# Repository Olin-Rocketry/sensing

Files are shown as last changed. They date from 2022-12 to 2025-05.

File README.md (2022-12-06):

# Sensing

Repository for all Olin Rocketry hardware and firmware.

The purpose of the avionics system is to determine when to deploy the drogue and main chutes, and to send the signal to do so to the recovery system. The flight computer contains several sensors to help detect apogee, and a microcontroller to read and process the data and send the signal.

The avionics system consists of

- a commercial-off-the-shelf (COTS) flight computer;
- a student-designed flight computer, which includes sensors, microcontroller, GPS, and radio; and
- a student-designed battery management system (BMS).

The COTS computer is a **\_** model. It has its own batteries, sensors, and radio and can trigger the recovery system independently. It is intended as a backup and is required by IREC competition rules (partly so they have a reliable altitude measurement for the competition). The BMS is described on the Power Management subteam page. It can suppy a steady 3.3V current up to about 1000 mA to the student-designed flight computer board.

**The flight computer consists of a Teensy 3.6 microcontroller and various sensors.**

- The [Teensy 3.6](https://www.pjrc.com/teensy/card9a_rev1.pdf) is computationally powerful enough for complex data processing, has many interrupt pins, and many pins in general for connecting multiple sensors. It also has a built-in SD card reader. The decision to use it was made before the Fall 2020 semester; other options were considered and may be viable for future iterations. The main drawback of the Teensy 3.6 is its cost, at around $30. This makes having multiple prototypes very expensive, especially if we want to distribute copies to team members living in separate places.
- We considered 3 different inertial measurement units (IMUs, or accelerometers):
  - [ADXL345](https://www.analog.com/media/en/technical-documentation/data-sheets/ADXL345.pdf) is a very common 3-axis accelerometer. It is widely available and was already in stock from JLC, the company manufacturing our board. This means our boards will have the ADXL345 already populated when it is shipped to us, a bonus.
  - [BMI088](https://download.mikroe.com/documents/datasheets/BMI088_Datasheet.pdf) is a 6-axis accelerometer and gyroscope (axes 4-6 are angular acceleration).
  - [BNO055](https://cdn-shop.adafruit.com/datasheets/BST_BNO055_DS000_12.pdf) is a 9-axis accelerometer, relative, and absolute gyroscope (axes 7-9 are absolute orientation).

We designed our Rev1 PCB to hold all three IMUs, so that we could test all of them at once. However, as of ordering time in January, the BMI088 and BNO055 were out of stock at Digikey and Mouser, so these were never tested.

- [MPL3115A2](https://www.nxp.com/docs/en/data-sheet/MPL3115A2.pdf) is a barometer calibrated to provide altimetry. It is the most important sensor, as it allows us to determine our absolute altitude. Our simplest apogee detection is triggered by a certain number of consecutive decreasing altitude measurements.
- Header pins for the [Adafruit Ultimate GPS Breakout (Version 3)](https://www.adafruit.com/product/746?__hstc), a $40 complete GPS module.
- Header pins for the [RFM9X LoRa Packet Radio Breakout](https://learn.adafruit.com/adafruit-rfm69hcw-and-rfm96-rfm95-rfm98-lora-packet-padio-breakouts/arduino-wiring), the currenty preferred radio (see Communications subteam page).

**Rev 1 Testing Update: Spring 2021**

The sensors on Rev1 (the ADXL345 accelerometer and the MPL3115A2 barometer) work, and the data can be read over I2C. The current data format is a csv file with time since launch, x, y, and z acceleration, pressure, altitude, and temperature. The readings from the accelerometer have very little noise when at rest (the only test performed so far - others to follow soon). The barometer has some issues. First of all, it has an offset of about 1.7 atmospheres. When those 1.7 atm are subtracted out, however, it provides high precision and sensitivity. The altitude readings are off by the same offset, as I believe they are calculated from the barometer reading anyway. The temperature has some 20 degrees F offset and significant drift of 2-5 degrees F over a few minutes. More testing to follow.

I looked at the specs and realized that the ADXL345 and MPL3115A2 together consume less than 3 mA of current at their max. Since the Teensy can output 250 mA through those pins, I don’t see why to use an external power source; we can just use the 3.3V pins on the Teensy.
The tests I have done have been using the 3.3V pin as a power source.

**Tests performed 3/26/2021:**

**Power supply test:** Get an external power supply and give 3.3V to the power inputs. Test the test points and the Teensy’s Vin pin. Test data logging onto SD card. Test sensors connected only to external power supply vs. connected to Teensy 3.3V pin vs. connected to both.

**Results:**
The transistor part of the Rev1 power management circuit did not work. For some reason, there was always only ~0.6V on both the gate and drain pins, and so 0.6V on the rest of the PCB. I tried several pin configurations and nothing helped. It worked fine when I bypassed the transistor and powered 3.3V to both the Teensy and the PCB.
The Teensy could not write to the SD card when the PCB and Teensy were powered independently; it only works when the rest of the PCB is powered through the Teensy’s dedicated 3.3V pin. Therefore, I recommend just using the Teensy’s 3.3V pin to power the sensors.

In this case, I suggest the voltage supplied by the BMS should be 3.6V instead of 3.3V, so that the linear voltage regulator on the Teensy can effectively supply the 3.3V to the sensors. Voltage regulators necessariy have a small voltage drop across them, although I came across a [source](https://forum.pjrc.com/threads/55789-Power-Teensy-3-6-with-lipo-battery?p=203568&viewfull=1#post203568) that says the Teensy will bypass its voltage regulator if the voltage is too low, so there is not necessarily an issue.

**MPL3115A2 Accuracy Test:** Take the Rev1 board up and down the stairs of the MAC building 2 times and measure altitude difference.

**Results:**
The readings are inaccurate, yet very precise. The pressure has reads on the order of 200 kPa, which is double what is expected (1 atmosphere is about 100 kPa), and the temperature reads 90 degrees F in a 70 degree room. Yet after the offset is subtracted, the sensor tracks changes in height of less than 20 feet (the distance between floors in the MAC, and the highest resolution analyzed) quite well. The graph below shows the corrected elevation and temperature over the course of my trip up and down the stairs of the MAC, then outside onto the great lawn and up to the 4th floor of West Hall. There is some drift over time as it sat on my desk after “landing,” on the order of 20 feet over 20 minutes. This is worrying, but it will likely not be a problem during a launch lasting a few minutes.

rev1 full schematic

**Developing the Rev 2 board**

With the ADXL345 and MPL3115A2 sensors confirmed to work, the main objective of the Rev 2 board is to make it fit into the avionics bay. The final board is 80mm tall by 72mm wide and has a mounting hole in each corner. The power supply transistor circuit has been replaced with a power multiplexer, a zener diode was added for overvoltage protection, and the power from the BMS goes directly into the Vin pin on the Teensy; the sensors and other circuitry are powered by the Teensy's 3.3V pin as discussed above. Additionally, 5 debugging LEDs, one power LED, and a [buzzer](https://www.digikey.com/en/products/detail/mallory-sonalert-products-inc/PT-1340P-P10-PQ/4996070) have also been added and are controlled by spare digital pins on the Teensy. A 10uF capacitor was added between the power and ground pins of the radio upon testing by the Communications team.

The board has been ordered from JLC and will arrive within a couple days.

## Guide to creating PCBs

**The process for creating the flight computer PCB has multiple stages:**
  1. Components are selected, including the microcontroller and sensors.
  2. Schematics are created for each sensor individually. This mainly involves copying the circuit diagram from the datasheets for each sensor. Every sensor needs at least two capacitors for its power source, and some require external pull-up resistors, for example. The BNO055 is connected to an external crystal oscillator. It’s also a good idea to add test points (basically large, labelled vias) for debugging purposes. We tried to add a test point to every trace on the schematic that would not be directly connected to the microcontroller (because we can access those traces directly through the microcontroller’s pins). 
  3. For the Rev1 board, footprints for the BNO055 and MPL3115A2 were created by copying the dimensions given by the datasheets. The other footprints were downloaded from snapeda.com. In reality, the only reason to create them manually is to get practice with KiCAD, which is why it was done this way for two of the sensors; in future, snapeda.com likely has all the footprints we will need, without the possibility of human error.*
  4. At this stage, layouts are also created for the supporting circuitry surrounding each sensor individually. These layouts will be manually recreated later, but it is easier to go through a few iterations to find the optimal footprint placements now, before all the layouts are combined on one board.
  5. Now, all of the individual schematics are moved into one place. This can be done in the KiCAD schematic editor (eeschema) by clicking File -> Append Schematic Sheet Content -> then navigate to the schematic to import and click Use Relative Path.
  6. Now all the schematics can be hooked up together; in this case it means connecting each sensor’s communication pins to the Teensy and power and ground to the power supply. A small circuit for regulating the power supply from the BMS, as well as header pins for the BMS and GPS and radio breakout boards are also added to this schematic.
  7. Review the schematics with the flight computer sub-team. Hopefully we have been checking in all along, but now is the last chance to make changes before a lot of work goes into the layout. After this, even small changes to the schematic can be very hard to implement in the layout without starting over.
  8. The layout of all the components for the final PCB is created. You cannot copy and paste the layouts created earlier for individual sensors, but you can follow the prior layouts as a guide. For the Rev1 board, we kept the components in the same relative orientation but did not pack them as closely together, to make debugging and potential fixes easier. During the layout process, it will probably make sense to swap the order of some pins connected to the microcontroller, in order to untangle the traces, or reduce the number of times traces have to cross over. Most pins on the Teensy 3.6 can function in the same way, so switching which pins are connected to which sensor is not a problem. Be careful not to switch the order of SCK and SDA; MISO and MOSI; or RX and TX; these pins are not interchangeable.
  9. It's a good idea to add filled zones on the front and back of the board. Having filled zones helps reduce signal noise and is standard practice. It also means there are fewer traces you have to draw. I usually make my filled zones be ground on both sides of the PCB, with an abundance of vias throughout the board to connect the front and back ground planes. Remember to press 'B' to redraw the zones in KiCAD.
  10. When the layout is done and reviewed, it is sent to JLC, our manufacturer. JLC can populate the PCB with basic components like capacitors, resistors, and even the ADXL345. They did not have any of the other sensors in stock, so we will solder those on campus. We will also solder header pins and large components like the power-regulating MOSFET transistor (which will be discontinued in Rev2).
  11. Next up is writing the firmware to test the sensors and hopefully getting some data!

\* In fact, I did make a very significant error while copying the footprint from the datasheet for both the BNO055 and the MPL3115. I copied the pads as they were shown in the datasheet, which was a bottom-up view. What matters for the layout is the top-down view (think about how the sensor sits on the PCB; you want to design the pads so they sit directly beneath the sensor). When you design the pads using the bottom-up view, you get a mirror image of how they are supposed to be. Moreover, since the footprints are often symmetrical, it can be impossible to tell you’ve made a mistake, until you realize that the pins things are supposed to be connected to are actually on the opposite side of the chip.

### Rev2 images

**Rev2 full schematic**

rev2 full schematic

**Rev2 power supply**

rev1 power supply

**Rev2 layout**

rev1 layout

**Rev2 3D model (front)**

rev1 3D model front

**Rev2 3D model (back)**

rev1 3D model back

### Rev1 images

**Rev1 full schematic**

rev1 full schematic

**Rev1 power supply**

rev1 power supply

**Rev1 layout**

rev1 layout

**Rev1 3D model (front)**

rev1 3D model front

**Rev1 3D model (back)**

rev1 3D model back

## Ordering PCBs From JLCPCB

For ordering the boards, go to JLCPCB.com (https://jlcpcb.com/RAT), and click on "Quote Now" button.

jlcpcb quote

JLCPCB (ShenzhenJLC Electronics Co., Ltd.), is the largest PCB prototype enterprise in China, and a high-tech manufacturer specializing in quick PCB prototype and small-batch PCB production. You can order a minimum of 5 PCBs for just $2.

First: Upload the gerber files for the board by clicking the "Add gerber file" button. You’ll notice a message at the bottom if the file is successfully uploaded.

jlcpbc gerber

A correctly uploaded gerber folder renders the board as follows:

jlcpcb render

Second: In order to get the board assembled (optional, based on the project requirements), select the "SMT Assembly option. It is important to select the side of the PCB that needs to be assembled, as well as the quantity for SMT. Press the "Confirm" button, then press the "Next" button.

jlcpcb smt

Third: upload the BOM (Bill of Material) and CPL (Component Placement List) files and click the "Next" button. It is necessary to make sure that each of these files follow the jlcpcb specified BOM and CPL formats, respectively:

- [Sample BOM](https://jlcpcb.com//video/JLCSMT_Sample_BOM1.xlsx?_ga=2.42560357.1905056644.1612161700-100444678.1610257845)
- [Sample CPL](https://jlcpcb.com//video/JLCSMT_Sample_CPL1.xlsx?_ga=2.42560357.1905056644.1612161700-100444678.1610257845)
- [SMT FAQ's](https://support.jlcpcb.com/category/78-smt-assembly?_ga=2.42560357.1905056644.1612161700-100444678.1610257845)

Note: If there is an issue with the BOM/CPL formatting, the the page will keep erroring out until it is resolved.

jlcpcb bom

Fourth: The parts are automatically detected through the uploaded BOM. They are also matched against jlcpcb's in-stock parts. It is important to go through each row and confirm if the auto-detected parts are the desired parts. Some parts will remain undetected if they cannot be assembled through SMT and require manual assembly post-deilvery.

jlcpcb parts

Fifth: The website renders an assembled board using the CPL file. This feature can be used to review the placement of the components (including orientation). Once carefull reviewed, the next step is to download a list of parts remaining to be assembled towards the bottom of this page view. It is important to place an order for the remaining components to be manually assembled upon delivery.

jlcpcb review

Sixth: Click on the “Save to Cart” button. Then, click on the "Secure Checkout" button.

jlcpcb checkout

Last: Add the payment details and choose the suitable delivery method (this includes FedEx, DHL, and standard mail options). Then, place the order.

Optional: To review the production status of the board, click on the "Order History" button under username. Then, click on In Production > view progress to obtain timestamps for each of the production steps in real time.

jlcpcb production

jlcpcb production progress

**Design Reviews**

-November 11, 2022 6:00 PM (done)

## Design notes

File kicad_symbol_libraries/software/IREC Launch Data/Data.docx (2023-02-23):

0

RSSI: -102

Got: Time: 14091326 Phase: 2 Arm: 1299.062500 Main: 1741.262451 Alt: 1284.187500

RSSI: -102

Got: Time: 140914500

RSSI: -102

Got: Time: 14091326 Phase: 2 Arm: 1299.062500 Main: 1741.262451 Alt: 1284.187500

RSSI: -102

Got: Time: 140914500

RSSI: -102

Got: Time: 14091326 Phase: 2 Arm: 1299.062500 Main: 1741.262451 Alt: 1284.187500

RSSI: -102

Got: Time: 140914Arduino LoRa RX Test!

LoRa radio init OK!

Set Freq to: 915.00

Got: Time: 14093661 Phase: 2 Arm: 1299.062500 Main: 1741.262451 Alt: 1284.312500

RSSI: -103

Got: Time: 14093828 Phase: 2 Arm: 1299.062500 Main: 1741.262451 Alt: 1284.312500

RSSI: -102

Got: Time: 14093994 Phase: 2 Arm: 1299.062500 Main: 1741.262451 Alt: 1284.250000

RSSI: -102

Got: Time: 14094161 Phase: 2 Arm: 1299.062500 Main: 1741.262451 Alt: 1284.125000

RSSI: -102

Got: Time: 14094328 Phase: 2 Arm: 1299.062500 Main: 1741.262451 Alt: 1283.437500

RSSI: -101

Got: Time: 14094495 Phase: 2 Arm: 1299.062500 Main: 1741.262451 Alt: 1284.625000

RSSI: -102

Got: Time: 14094661 Phase: 2 Arm: 1299.062500 Main: 1741.262451 Alt: 1284.312500

RSSI: -103

Got: Time: 14094828 Phase: 2 Arm: 1299.062500 Main: 1741.262451 Alt: 1284.312500

RSSI: -103

Got: Time: 14094995 Phase: 2 Arm: 1299.062500 Main: 1741.262451 Alt: 1284.375000

RSSI: -102

Got: Time: 14095162 Phase: 2 Arm: 1299.062500 Main: 1741.262451 Alt: 1283.937500

RSSI: -99

Got: Time: 14095329 Phase: 2 Arm: 1299.062500 Main: 1741.262451 Alt: 1284.187500

RSSI: -103

Got: Time: 14095495 Phase: 2 Arm: 1299.062500 Main: 1741.262451 Alt: 1284.187500

RSSI: -103

Got: Time: 14095662 Phase: 2 Arm: 1299.062500 Main: 1741.262451 Alt: 1284.437500

RSSI: -103

Got: Time: 14095829 Phase: 2 Arm: 1299.062500 Main: 1741.262451 Alt: 1283.875000

RSSI: -103

Got: Time: 14095996 Phase: 2 Arm: 1299.062500 Main: 1741.262451 Alt: 1284.375000

RSSI: -102

Got: Time: 14096162 Phase: 2 Arm: 1299.062500 Main: 1741.262451 Alt: 1283.937500

RSSI: -101

Got: Time: 14096329 Phase: 2 Arm: 1299.062500 Main: 1741.262451 Alt: 1284.187500

RSSI: -102

Got: Time: 14096496 Phase: 2 Arm: 1299.062500 Main: 1741.262451 Alt: 1283.937500

RSSI: -102

Got: Time: 14096663 Phase: 2 Arm: 1299.062500 Main: 1741.262451 Alt: 1284.000000

RSSI: -103

Got: Time: 14096829 Phase: 2 Arm: 1299.062500 Main: 1741.262451 Alt: 1284.125000

RSSI: -102

Got: Time: 14096996 Phase: 2 Arm: 1299.062500 Main: 1741.262451 Alt: 1284.312500

RSSI: -103

Got: Time: 14097163 Phase: 2 Arm: 1299.062500 Main: 1741.262451 Alt: 1283.812500

RSSI: -99

Got: Time: 14097330 Phase: 2 Arm: 1299.062500 Main: 1741.262451 Alt: 1284.375000

RSSI: -102

Got: Time: 14097497 Phase: 2 Arm: 1299.062500 Main: 1741.262451 Alt: 1283.562500

RSSI: -102

Got: Time: 14097663 Phase: 2 Arm: 1299.062500 Main: 1741.262451 Alt: 1283.937500

RSSI: -103

Got: Time: 14097830 Phase: 2 Arm: 1299.062500 Main: 1741.262451 Alt: 1284.375000

RSSI: -103

Got: Time: 14097997 Phase: 2 Arm: 1299.062500 Main: 1741.262451 Alt: 1284.125000

RSSI: -103

Got: Time: 14098164 Phase: 2 Arm: 1299.062500 Main: 1741.262451 Alt: 1284.312500

RSSI: -98

Got: Time: 14098330 Phase: 2 Arm: 1299.062500 Main: 1741.262451 Alt: 1284.187500

RSSI: -103

Got: Time: 14098497 Phase: 2 Arm: 1299.062500 Main: 1741.262451 Alt: 1284.187500

RSSI: -102

Got: Time: 14098664 Phase: 2 Arm: 1299.062500 Main: 1741.262451 Alt: 1283.937500

RSSI: -103

Got: Time: 14098831 Phase: 2 Arm: 1299.062500 Main: 1741.262451 Alt: 1283.875000

RSSI: -102

Got: Time: 14098997 Phase: 2 Arm: 1299.062500 Main: 1741.262451 Alt: 1283.937500

RSSI: -103

Got: Time: 14099164 Phase: 2 Arm: 1299.062500 Main: 1741.262451 Alt: 1283.312500

RSSI: -100

Got: Time: 14099331 Phase: 2 Arm: 1299.062500 Main: 1741.262451 Alt: 1283.312500

RSSI: -99

Got: Time: 14099498 Phase: 2 Arm: 1299.062500 Main: 1741.262451 Alt: 1283.750000

RSSI: -102

Got: Time: 14099665 Phase: 2 Arm: 1299.062500 Main: 1741.262451 Alt: 1283.562500

RSSI: -102

Got: Time: 14099831 Phase: 2 Arm: 1299.062500 Main: 1741.262451 Alt: 1284.187500

RSSI: -102

Got: Time: 14099998 Phase: 2 Arm: 1299.062500 Main: 1741.262451 Alt: 1283.937500

RSSI: -102

Got: Time: 14100165 Phase: 2 Arm: 1299.062500 Main: 1741.262451 Alt: 1284.000000

RSSI: -102

Got: Time: 14100332 Phase: 2 Arm: 1299.062500 Main: 1741.262451 Alt: 1284.062500

RSSI: -103

Got: Time: 14100498 Phase: 2 Arm: 1299.062500 Main: 1741.262451 Alt: 1284.062500

RSSI: -102

Got: Time: 14100665 Phase: 2 Arm: 1299.062500 Main: 1741.262451 Alt: 1283.937500

RSSI: -103

Got: Time: 14100832 Phase: 2 Arm: 1299.062500 Main: 1741.262451 Alt: 1283.875000

RSSI: -103

Got: Time: 14100999 Phase: 2 Arm: 1299.062500 Main: 1741.262451 Alt: 1283.937500

RSSI: -103

Got: Time: 14101165 Phase: 2 Arm: 1299.062500 Main: 1741.262451 Alt: 1284.375000

RSSI: -101

Got: Time: 14101332 Phase: 2 Arm: 1299.062500 Main: 1741.262451 Alt: 1284.000000

RSSI: -103

Got: Time: 14101499 Phase: 2 Arm: 1299.062500 Main: 1741.262451 Alt: 1284.187500

RSSI: -102

Got: Time: 14101666 Phase: 2 Arm: 1299.062500 Main: 1741.262451 Alt: 1284.062500

RSSI: -102

Got: Time: 14101832 Phase: 2 Arm: 1299.062500 Main: 1741.262451 Alt: 1284.000000

RSSI: -102

Got: Time: 14101999 Phase: 2 Arm: 1299.062500 Main: 1741.262451 Alt: 1284.562500

RSSI: -103

Got: Time: 14102166 Phase: 2 Arm: 1299.062500 Main: 1741.262451 Alt: 1283.937500

RSSI: -99

Got: Time: 14102333 Phase: 2 Arm: 1299.062500 Main: 1741.262451 Alt: 1283.562500

RSSI: -102

Got: Time: 14102500 Phase: 2 Arm: 1299.062500 Main: 1741.262451 Alt: 1283.750000

RSSI: -102

Got: Time: 14102666 Phase: 2 Arm: 1299.062500 Main: 1741.262451 Alt: 1284.062500

RSSI: -102

Got: Time: 14102833 Phase: 2 Arm: 1299.062500 Main: 1741.262451 Alt: 1284.375000

RSSI: -102

Got: Time: 14103000 Phase: 2 Arm: 1299.062500 Main: 1741.262451 Alt: 1283.937500

RSSI: -102

Got: Time: 14103167 Phase: 2 Arm: 1299.062500 Main: 1741.262451 Alt: 1284.375000

RSSI: -100

Got: Time: 14103333 Phase: 2 Arm: 1299.062500 Main: 1741.262451 Alt: 1283.625000

RSSI: -102

Got: Time: 14103500 Phase: 2 Arm: 1299.062500 Main: 1741.262451 Alt: 1283.375000

RSSI: -102

Got: Time: 14103667 Phase: 2 Arm: 1299.062500 Main: 1741.262451 Alt: 1283.750000

RSSI: -102

Got: Time: 14103834 Phase: 2 Arm: 1299.062500 Main: 1741.262451 Alt: 1284.375000

RSSI: -102

Got: Time: 14104000 Phase: 2 Arm: 1299.062500 Main: 1741.262451 Alt: 1283.562500

RSSI: -102

Got: Time: 14104167 Phase: 2 Arm: 1299.062500 Main: 1741.262451 Alt: 1283.875000

RSSI: -100

Got: Time: 14104334 Phase: 2 Arm: 1299.062500 Main: 1741.262451 Alt: 1284.250000

RSSI: -100

Got: Time: 14104501 Phase: 2 Arm: 1299.062500 Main: 1741.262451 Alt: 1284.187500

RSSI: -102

Got: Time: 14104668 Phase: 2 Arm: 1299.062500 Main: 1741.262451 Alt: 1284.187500

RSSI: -103

Got: Time: 14104834 Phase: 2 Arm: 1299.062500 Main: 1741.262451 Alt: 1284.562500

RSSI: -102

Got: Time: 14105001 Phase: 2 Arm: 1299.062500 Main: 1741.262451 Alt: 1283.812500

RSSI: -102

Got: Time: 14105168 Phase: 2 Arm: 1299.062500 Main: 1741.262451 Alt: 1284.375000

RSSI: -96

Got: Time: 14105335 Phase: 2 Arm: 1299.062500 Main: 1741.262451 Alt: 1283.937500

RSSI: -102

Got: Time: 14105501 Phase: 2 Arm: 1299.062500 Main: 1741.262451 Alt: 1284.312500

RSSI: -102

Got: Time: 14105668 Phase: 2 Arm: 1299.062500 Main: 1741.262451 Alt: 1283.937500

RSSI: -102

Got: Time: 14105835 Phase: 2 Arm: 1299.062500 Main: 1741.262451 Alt: 1284.000000

RSSI: -102

Got: Time: 14106002 Phase: 2 Arm: 1299.062500 Main: 1741.262451 Alt: 1284.562500

RSSI: -102

Got: Time: 14106168 Phase: 2 Arm: 1299.062500 Main: 1741.262451 Alt: 1283.687500

RSSI: -98

Got: Time: 14106335 Phase: 2 Arm: 1299.062500 Main: 1741.262451 Alt: 1284.187500

RSSI: -102

Got: Time: 14106502 Phase: 2 Arm: 1299.062500 Main: 1741.262451 Alt: 1283.750000

RSSI: -102

Got: Time: 14106669 Phase: 2 Arm: 1299.062500 Main: 1741.262451 Alt: 1283.937500

RSSI: -103

Got: Time: 14106836 Phase: 2 Arm: 1299.062500 Main: 1741.262451 Alt: 1284.375000

RSSI: -103

Got: Time: 14107002 Phase: 2 Arm: 1299.062500 Main: 1741.262451 Alt: 1283.937500

RSSI: -102

Got: Time: 14107169 Phase: 2 Arm: 1299.062500 Main: 1741.262451 Alt: 1283.750000

RSSI: -97

Got: Time: 14107336 Phase: 2 Arm: 1299.062500 Main: 1741.262451 Alt: 1284.062500

RSSI: -102

Got: Time: 14107503 Phase: 2 Arm: 1299.062500 Main: 1741.262451 Alt: 1284.375000

RSSI: -102

Got: Time: 14107669 Phase: 2 Arm: 1299.062500 Main: 1741.262451 Alt: 1283.562500

RSSI: -102

Got: Time: 14107836 Phase: 2 Arm: 1299.062500 Main: 1741.262451 Alt: 1284.250000

RSSI: -103

Got: Time: 14108170 Phase: 2 Arm: 1299.062500 Main: 1741.262451 Alt: 1283.937500

RSSI: -101

Got: Time: 14108336 Phase: 2 Arm: 1299.062500 Main: 1741.262451 Alt: 1283.937500

RSSI: -102

Got: Time: 14108503 Phase: 2 Arm: 1299.062500 Main: 1741.262451 Alt: 1284.500000

RSSI: -102

Got: Time: 14108670 Phase: 2 Arm: 1299.062500 Main: 1741.262451 Alt: 1283.687500

RSSI: -102

Got: Time: 14108837 Phase: 2 Arm: 1299.062500 Main: 1741.262451 Alt: 1284.125000

RSSI: -102

Got: Time: 14109004 Phase: 2 Arm: 1299.062500 Main: 1741.262451 Alt: 1284.000000

RSSI: -102

Got: Time: 14109170 Phase: 2 Arm: 1299.062500 Main: 1741.262451 Alt: 1283.937500

RSSI: -101

Got: Time: 14109337 Phase: 2 Arm: 1299.062500 Main: 1741.262451 Alt: 1284.500000

RSSI: -102

Got: Time: 14109504 Phase: 2 Arm: 1299.062500 Main: 1741.262451 Alt: 1284.187500

RSSI: -102

Got: Time: 14109671 Phase: 2 Arm: 1299.062500 Main: 1741.262451 Alt: 1284.562500

RSSI: -102

Got: Time: 14109837 Phase: 2 Arm: 1299.062500 Main: 1741.262451 Alt: 1284.125000

RSSI: -102

Got: Time: 14110004 Phase: 2 Arm: 1299.062500 Main: 1741.262451 Alt: 1284.375000

RSSI: -103

Got: Time: 14110171 Phase: 2 Arm: 1299.062500 Main: 1741.262451 Alt: 1284.500000

RSSI: -101

Got: Time: 14110338 Phase: 2 Arm: 1299.062500 Main: 1741.262451 Alt: 1284.312500

RSSI: -102

Got: Time: 14110504 Phase: 2 Arm: 1299.062500 Main: 1741.262451 Alt: 1284.187500

RSSI: -102

Got: Time: 14110671 Phase: 2 Arm: 1299.062500 Main: 1741.262451 Alt: 1283.750000

RSSI: -102

Got: Time: 14110838 Phase: 2 Arm: 1299.062500 Main: 1741.262451 Alt: 1283.687500

RSSI: -102

Got: Time: 14111005 Phase: 2 Arm: 1299.062500 Main: 1741.262451 Alt: 1283.562500

RSSI: -102

Got: Time: 14111172 Phase: 2 Arm: 1299.062500 Main: 1741.262451 Alt: 1283.750000

RSSI: -102

Got: Time: 14111338 Phase: 2 Arm: 1299.062500 Main: 1741.262451 Alt: 1284.687500

RSSI: -102

Got: Time: 14111505 Phase: 2 Arm: 1299.062500 Main: 1741.262451 Alt: 1283.750000

RSSI: -102

Got: Time: 14111672 Phase: 2 Arm: 1299.062500 Main: 1741.262451 Alt: 1284.062500

RSSI: -102

Got: Time: 14111839 Phase: 2 Arm: 1299.062500 Main: 1741.262451 Alt: 1283.812500

RSSI: -102

Got: Time: 14112005 Phase: 2 Arm: 1299.062500 Main: 1741.262451 Alt: 1284.187500

RSSI: -102

Got: Time: 14112172 Phase: 2 Arm: 1299.062500 Main: 1741.262451 Alt: 1284.750000

RSSI: -101

Got: Time: 14112339 Phase: 2 Arm: 1299.062500 Main: 1741.262451 Alt: 1284.187500

RSSI: -102

Got: Time: 14112506 Phase: 2 Arm: 1299.062500 Main: 1741.262451 Alt: 1284.187500

RSSI: -102

Got: Time: 14112672 Phase: 2 Arm: 1299.062500 Main: 1741.262451 Alt: 1283.750000

RSSI: -102

Got: Time: 14112839 Phase: 2 Arm: 1299.062500 Main: 1741.262451 Alt: 1284.187500

RSSI: -102

Got: Time: 14113006 Phase: 2 Arm: 1299.062500 Main: 1741.262451 Alt: 1284.562500

RSSI: -102

Got: Time: 14113173 Phase: 2 Arm: 1299.062500 Main: 1741.262451 Alt: 1284.125000

RSSI: -100

Got: Time: 14113339 Phase: 2 Arm: 1299.062500 Main: 1741.262451 Alt: 1283.937500

RSSI: -102

Got: Time: 14113506 Phase: 2 Arm: 1299.062500 Main: 1741.262451 Alt: 1283.937500

RSSI: -102

Got: Time: 14113673 Phase: 2 Arm: 1299.062500 Main: 1741.262451 Alt: 1283.750000

RSSI: -102

Got: Time: 14113840 Phase: 2 Arm: 1299.062500 Main: 1741.262451 Alt: 1284.187500

RSSI: -102

Got: Time: 14114007 Phase: 2 Arm: 1299.062500 Main: 1741.262451 Alt: 1283.250000

RSSI: -102

Got: Time: 14114173 Phase: 2 Arm: 1299.062500 Main: 1741.262451 Alt: 1284.562500

RSSI: -101

Got: Time: 14114340 Phase: 2 Arm: 1299.062500 Main: 1741.262451 Alt: 1284.437500

RSSI: -101

Got: Time: 14114507 Phase: 2 Arm: 1299.062500 Main: 1741.262451 Alt: 1283.750000

RSSI: -102

Got: Time: 14114674 Phase: 2 Arm: 1299.062500 Main: 1741.262451 Alt: 1284.750000

RSSI: -102

Got: Time: 14114840 Phase: 2 Arm: 1299.062500 Main: 1741.262451 Alt: 1284.250000

RSSI: -102

Got: Time: 14115007 Phase: 2 Arm: 1299.062500 Main: 1741.262451 Alt: 1284.250000

RSSI: -102

Got: Time: 14115174 Phase: 2 Arm: 1299.062500 Main: 1741.262451 Alt: 1283.687500

RSSI: -98

Got: Time: 14115341 Phase: 2 Arm: 1299.062500 Main: 1741.262451 Alt: 1284.062500

RSSI: -102

Got: Time: 14115507 Phase: 2 Arm: 1299.062500 Main: 1741.262451 Alt: 1284.375000

RSSI: -102

Got: Time: 14115674 Phase: 2 Arm: 1299.062500 Main: 1741.262451 Alt: 1284.187500

RSSI: -102

Got: Time: 14115841 Phase: 2 Arm: 1299.062500 Main: 1741.262451 Alt: 1284.687500

RSSI: -102

Got: Time: 14116008 Phase: 2 Arm: 1299.062500 Main: 1741.262451 Alt: 1284.375000

RSSI: -102

Got: Time: 14116175 Phase: 2 Arm: 1299.062500 Main: 1741.262451 Alt: 1284.187500

RSSI: -97

Got: Time: 14116341 Phase: 2 Arm: 1299.062500 Main: 1741.262451 Alt: 1284.000000

RSSI: -102

Got: Time: 14116508 Phase: 2 Arm: 1299.062500 Main: 1741.262451 Alt: 1284.812500

RSSI: -102

Got: Time: 14116675 Phase: 2 Arm: 1299.062500 Main: 1741.262451 Alt: 1284.250000

RSSI: -102

Got: Time: 14116842 Phase: 2 Arm: 1299.062500 Main: 1741.262451 Alt: 1284.500000

RSSI: -103

Got: Time: 14117008 Phase: 2 Arm: 1299.062500 Main: 1741.262451 Alt: 1284.375000

RSSI: -102

Got: Time: 14117175 Phase: 2 Arm: 1299.062500 Main: 1741.262451 Alt: 1283.937500

RSSI: -98

Got: Time: 14117342 Phase: 2 Arm: 1299.062500 Main: 1741.262451 Alt: 1283.812500

RSSI: -102

Got: Time: 14117509 Phase: 2 Arm: 1299.062500 Main: 1741.262451 Alt: 1284.125000

RSSI: -102

Got: Time: 14117675 Phase: 2 Arm: 1299.062500 Main: 1741.262451 Alt: 1284.187500

RSSI: -102

Got: Time: 14117842 Phase: 2 Arm: 1299.062500 Main: 1741.262451 Alt: 1284.375000

RSSI: -102

Got: Time: 14118009 Phase: 2 Arm: 1299.062500 Main: 1741.262451 Alt: 1284.000000

RSSI: -102

Got: Time: 14118176 Phase: 2 Arm: 1299.062500 Main: 1741.262451 Alt: 1283.937500

RSSI: -97

Got: Time: 14118343 Phase: 2 Arm: 1299.062500 Main: 1741.262451 Alt: 1283.750000

RSSI: -102

Got: Time: 14118509 Phase: 2 Arm: 1299.062500 Main: 1741.262451 Alt: 1283.750000

RSSI: -102

Got: Time: 14118676 Phase: 2 Arm: 1299.062500 Main: 1741.262451 Alt: 1284.562500

RSSI: -102

Got: Time: 14118843 Phase: 2 Arm: 1299.062500 Main: 1741.262451 Alt: 1284.125000

RSSI: -102

Got: Time: 14119010 Phase: 2 Arm: 1299.062500 Main: 1741.262451 Alt: 1284.437500

RSSI: -102

Got: Time: 14119176 Phase: 2 Arm: 1299.062500 Main: 1741.262451 Alt: 1284.312500

RSSI: -98

Got: Time: 14119343 Phase: 2 Arm: 1299.062500 Main: 1741.262451 Alt: 1283.937500

RSSI: -100

Got: Time: 14119510 Phase: 2 Arm: 1299.062500 Main: 1741.262451 Alt: 1283.687500

RSSI: -103

Got: Time: 14119677 Phase: 2 Arm: 1299.062500 Main: 1741.262451 Alt: 1284.187500

RSSI: -103

Got: Time: 14119843 Phase: 2 Arm: 1299.062500 Main: 1741.262451 Alt: 1284.375000

RSSI: -103

Got: Time: 14120177 Phase: 2 Arm: 1299.062500 Main: 1741.262451 Alt: 1284.312500

RSSI: -99

Got: Time: 14120344 Phase: 2 Arm: 1299.062500 Main: 1741.262451 Alt: 1284.562500

RSSI: -103

Got: Time: 14120510 Phase: 2 Arm: 1299.062500 Main: 1741.262451 Alt: 1284.937500

RSSI: -103

Got: Time: 14120677 Phase: 2 Arm: 1299.062500 Main: 1741.262451 Alt: 1284.312500

RSSI: -103

Got: Time: 14120844 Phase: 2 Arm: 1299.062500 Main: 1741.262451 Alt: 1284.562500

RSSI: -103

Got: Time: 14121011 Phase: 2 Arm: 1299.062500 Main: 1741.262451 Alt: 1284.437500

RSSI: -102

Got: Time: 14121178 Phase: 2 Arm: 1299.062500 Main: 1741.262451 Alt: 1284.687500

RSSI: -99

Got: Time: 14121344 Phase: 2 Arm: 1299.062500 Main: 1741.262451 Alt: 1284.562500

RSSI: -103

Got: Time: 14121511 Phase: 2 Arm: 1299.062500 Main: 1741.262451 Alt: 1284.375000

RSSI: -103

Got: Time: 14121678 Phase: 2 Arm: 1299.062500 Main: 1741.262451 Alt: 1284.375000

RSSI: -103

Got: Time: 14121845 Phase: 2 Arm: 1299.062500 Main: 1741.262451 Alt: 1283.937500

RSSI: -102

Got: Time: 14122011 Phase: 2 Arm: 1299.062500 Main: 1741.262451 Alt: 1284.375000

RSSI: -103

Got: Time: 14122178 Phase: 2 Arm: 1299.062500 Main: 1741.262451 Alt: 1284.125000

RSSI: -100

Got: Time: 14122345 Phase: 2 Arm: 1299.062500 Main: 1741.262451 Alt: 1283.875000

RSSI: -103

Got: Time: 14122512 Phase: 2 Arm: 1299.062500 Main: 1741.262451 Alt: 1284.375000

RSSI: -103

Got: Time: 14122678 Phase: 2 Arm: 1299.062500 Main: 1741.262451 Alt: 1284.000000

RSSI: -102

Got: Time: 14122845 Phase: 2 Arm: 1299.062500 Main: 1741.262451 Alt: 1283.812500

RSSI: -103

Got: Time: 14123012 Phase: 2 Arm: 1299.062500 Main: 1741.262451 Alt: 1284.250000

RSSI: -103

Got: Time: 14123179 Phase: 2 Arm: 1299.062500 Main: 1741.262451 Alt: 1284.062500

RSSI: -99

Got: Time: 14123346 Phase: 2 Arm: 1299.062500 Main: 1741.262451 Alt: 1283.875000

RSSI: -102

Got: Time: 14123512 Phase: 2 Arm: 1299.062500 Main: 1741.262451 Alt: 1283.937500

RSSI: -103

Got: Time: 14123679 Phase: 2 Arm: 1299.062500 Main: 1741.262451 Alt: 1283.625000

RSSI: -102

Got: Time: 14123846 Phase: 2 Arm: 1299.062500 Main: 1741.262451 Alt: 1284.187500

RSSI: -103

Got: Time: 14124013 Phase: 2 Arm: 1299.062500 Main: 1741.262451 Alt: 1284.562500

RSSI: -102

Got: Time: 14124179 Phase: 2 Arm: 1299.062500 Main: 1741.262451 Alt: 1284.187500

RSSI: -100

Got: Time: 14124346 Phase: 2 Arm: 1299.062500 Main: 1741.262451 Alt: 1283.937500

RSSI: -99

Got: Time: 14124513 Phase: 2 Arm: 1299.062500 Main: 1741.262451 Alt: 1284.375000

RSSI: -102

Got: Time: 14124680 Phase: 2 Arm: 1299.062500 Main: 1741.262451 Alt: 1284.187500

RSSI: -102

Got: Time: 14124846 Phase: 2 Arm: 1299.062500 Main: 1741.262451 Alt: 1284.062500

RSSI: -102

Got: Time: 14125013 Phase: 2 Arm: 1299.062500 Main: 1741.262451 Alt: 1284.187500

RSSI: -102

Got: Time: 14125180 Phase: 2 Arm: 1299.062500 Main: 1741.262451 Alt: 1284.250000

RSSI: -98

Got: Time: 14125347 Phase: 2 Arm: 1299.062500 Main: 1741.262451 Alt: 1284.187500

RSSI: -102

Got: Time: 14125514 Phase: 2 Arm: 1299.062500 Main: 1741.262451 Alt: 1284.375000

RSSI: -102

Got: Time: 14125680 Phase: 2 Arm: 1299.062500 Main: 1741.262451 Alt: 1283.937500

RSSI: -102

Got: Time: 14125847 Phase: 2 Arm: 1299.062500 Main: 1741.262451 Alt: 1284.437500

RSSI: -103

Got: Time: 14126014 Phase: 2 Arm: 1299.062500 Main: 1741.262451 Alt: 1284.187500

RSSI: -103

Got: Time: 14126181 Phase: 2 Arm: 1299.062500 Main: 1741.262451 Alt: 1284.250000

RSSI: -101

Got: Time: 14126347 Phase: 2 Arm: 1299.062500 Main: 1741.262451 Alt: 1283.875000

RSSI: -102

Got: Time: 14126514 Phase: 2 Arm: 1299.062500 Main: 1741.262451 Alt: 1284.375000

RSSI: -103

Got: Time: 14126681 Phase: 2 Arm: 1299.062500 Main: 1741.262451 Alt: 1284.187500

RSSI: -102

Got: Time: 14126848 Phase: 2 Arm: 1299.062500 Main: 1741.262451 Alt: 1283.500000

RSSI: -103

Got: Time: 14127014 Phase: 2 Arm: 1299.062500 Main: 1741.262451 Alt: 1284.375000

RSSI: -103

Got: Time: 14127181 Phase: 2 Arm: 1299.062500 Main: 1741.262451 Alt: 1283.937500

RSSI: -100

Got: Time: 14127348 Phase: 2 Arm: 1299.062500 Main: 1741.262451 Alt: 1283.750000

RSSI: -103

Got: Time: 14127515 Phase: 2 Arm: 1299.062500 Main: 1741.262451 Alt: 1284.312500

RSSI: -103

Got: Time: 14127682 Phase: 2 Arm: 1299.062500 Main: 1741.262451 Alt: 1284.000000

RSSI: -103

Got: Time: 14127848 Phase: 2 Arm: 1299.062500 Main: 1741.262451 Alt: 1284.312500

RSSI: -103

Got: Time: 14128015 Phase: 2 Arm: 1299.062500 Main: 1741.262451 Alt: 1283.812500

RSSI: -103

Got: Time: 14128182 Phase: 2 Arm: 1299.062500 Main: 1741.262451 Alt: 1284.187500

RSSI: -101

Got: Time: 14128349 Phase: 2 Arm: 1299.062500 Main: 1741.262451 Alt: 1283.875000

RSSI: -102

Got: Time: 14128515 Phase: 2 Arm: 1299.062500 Main: 1741.262451 Alt: 1284.625000

RSSI: -102

Got: Time: 14128682 Phase: 2 Arm: 1299.062500 Main: 1741.262451 Alt: 1283.937500

RSSI: -103

Got: Time: 14128849 Phase: 2 Arm: 1299.062500 Main: 1741.262451 Alt: 1284.375000

RSSI: -103

Got: Time: 14129016 Phase: 2 Arm: 1299.062500 Main: 1741.262451 Alt: 1284.500000

RSSI: -102

Got: Time: 14129182 Phase: 2 Arm: 1299.062500 Main: 1741.262451 Alt: 1284.187500

RSSI: -98

Got: Time: 14129349 Phase: 2 Arm: 1299.062500 Main: 1741.262451 Alt: 1284.250000

RSSI: -100

Got: Time: 14129516 Phase: 2 Arm: 1299.062500 Main: 1741.262451 Alt: 1284.250000

RSSI: -102

Got: Time: 14129683 Phase: 2 Arm: 1299.062500 Main: 1741.262451 Alt: 1284.250000

RSSI: -103

Got: Time: 14129849 Phase: 2 Arm: 1299.062500 Main: 1741.262451 Alt: 1284.562500

RSSI: -103

Got: Time: 14130016 Phase: 2 Arm: 1299.062500 Main: 1741.262451 Alt: 1284.375000

RSSI: -103

Got: Time: 14130183 Phase: 2 Arm: 1299.062500 Main: 1741.262451 Alt: 1283.812500

RSSI: -99

Got: Time: 14130350 Phase: 2 Arm: 1299.062500 Main: 1741.262451 Alt: 1284.437500

RSSI: -102

Got: Time: 14130517 Phase: 2 Arm: 1299.062500 Main: 1741.262451 Alt: 1285.000000

RSSI: -102

Got: Time: 14130683 Phase: 2 Arm: 1299.062500 Main: 1741.262451 Alt: 1284.437500

RSSI: -102

Got: Time: 14130850 Phase: 2 Arm: 1299.062500 Main: 1741.262451 Alt: 1284.375000

RSSI: -102

Got: Time: 14131017 Phase: 2 Arm: 1299.062500 Main: 1741.262451 Alt: 1283.937500

RSSI: -102

Got: Time: 14131184 Phase: 2 Arm: 1299.062500 Main: 1741.262451 Alt: 1284.500000

RSSI: -98

Got: Time: 14131350 Phase: 2 Arm: 1299.062500 Main: 1741.262451 Alt: 1283.562500

RSSI: -103

Got: Time: 14131517 Phase: 2 Arm: 1299.062500 Main: 1741.262451 Alt: 1284.750000

RSSI: -103

Got: Time: 14131684 Phase: 2 Arm: 1299.062500 Main: 1741.262451 Alt: 1284.062500

RSSI: -102

Got: Time: 14131851 Phase: 2 Arm: 1299.062500 Main: 1741.262451 Alt: 1283.812500

RSSI: -103

Got: Time: 14132017 Phase: 2 Arm: 1299.062500 Main: 1741.262451 Alt: 1284.375000

RSSI: -103

Got: Time: 14132184 Phase: 2 Arm: 1299.062500 Main: 1741.262451 Alt: 1283.125000

RSSI: -100

Got: Time: 14132351 Phase: 2 Arm: 1299.062500 Main: 1741.262451 Alt: 1283.562500

RSSI: -103

Got: Time: 14132518 Phase: 2 Arm: 1299.062500 Main: 1741.262451 Alt: 1284.000000

RSSI: -102

Got: Time: 14132685 Phase: 2 Arm: 1299.062500 Main: 1741.262451 Alt: 1284.187500

RSSI: -102

Got: Time: 14132851 Phase: 2 Arm: 1299.062500 Main: 1741.262451 Alt: 1283.562500

RSSI: -103

Got: Time: 14133018 Phase: 2 Arm: 1299.062500 Main: 1741.262451 Alt: 1283.937500

RSSI: -103

Got: Time: 14133185 Phase: 2 Arm: 1299.062500 Main: 1741.262451 Alt: 1284.312500

RSSI: -99

Got: Time: 14133352 Phase: 2 Arm: 1299.062500 Main: 1741.262451 Alt: 1283.625000

RSSI: -102

Got: Time: 14133518 Phase: 2 Arm: 1299.062500 Main: 1741.262451 Alt: 1284.562500

RSSI: -102

Got: Time: 14133685 Phase: 2 Arm: 1299.062500 Main: 1741.262451 Alt: 1284.062500

RSSI: -102

Got: Time: 14133852 Phase: 2 Arm: 1299.062500 Main: 1741.262451 Alt: 1284.375000

RSSI: -103

Got: Time: 14134019 Phase: 2 Arm: 1299.062500 Main: 1741.262451 Alt: 1283.875000

RSSI: -103

Got: Time: 14134185 Phase: 2 Arm: 1299.062500 Main: 1741.262451 Alt: 1284.375000

RSSI: -102

Got: Time: 14134352 Phase: 2 Arm: 1299.062500 Main: 1741.262451 Alt: 1283.937500

RSSI: -97

Got: Time: 14134519 Phase: 2 Arm: 1299.062500 Main: 1741.262451 Alt: 1283.812500

RSSI: -103

Got: Time: 14134686 Phase: 2 Arm: 1299.062500 Main: 1741.262451 Alt: 1284.625000

RSSI: -103

Got: Time: 14134853 Phase: 2 Arm: 1299.062500 Main: 1741.262451 Alt: 1284.312500

RSSI: -103

Got: Time: 14135019 Phase: 2 Arm: 1299.062500 Main: 1741.262451 Alt: 1284.312500

RSSI: -101

Got: Time: 14135186 Phase: 2 Arm: 1299.062500 Main: 1741.262451 Alt: 1284.562500

RSSI: -100

Got: Time: 14135353 Phase: 2 Arm: 1299.062500 Main: 1741.262451 Alt: 1283.937500

RSSI: -104

Got: Time: 14135520 Phase: 2 Arm: 1299.062500 Main: 1741.262451 Alt: 1284.250000

RSSI: -104

Got: Time: 14135686 Phase: 2 Arm: 1299.062500 Main: 1741.262451 Alt: 1284.187500

RSSI: -104

Got: Time: 14135853 Phase: 2 Arm: 1299.062500 Main: 1741.262451 Alt: 1284.000000

RSSI: -104

Got: Time: 14136020 Phase: 2 Arm: 1299.062500 Main: 1741.262451 Alt: 1283.937500

RSSI: -102

Got: Time: 14136187 Phase: 2 Arm: 1299.062500 Main: 1741.262451 Alt: 1284.562500

RSSI: -101

Got: Time: 14136353 Phase: 2 Arm: 1299.062500 Main: 1741.262451 Alt: 1283.125000

RSSI: -105

Got: Time: 14136520 Phase: 2 Arm: 1299.062500 Main: 1741.262451 Alt: 1284.062500

RSSI: -105

Got: Time: 14136687 Phase: 2 Arm: 1299.062500 Main: 1741.262451 Alt: 1284.375000

RSSI: -104

Got: Time: 14136854 Phase: 2 Arm: 1299.062500 Main: 1741.262451 Alt: 1283.937500

RSSI: -104

Got: Time: 14137020 Phase: 2 Arm: 1299.062500 Main: 1741.262451 Alt: 1284.062500

RSSI: -102

Got: Time: 14137187 Phase: 2 Arm: 1299.062500 Main: 1741.262451 Alt: 1284.375000

RSSI: -101

Got: Time: 14137354 Phase: 2 Arm: 1299.062500 Main: 1741.262451 Alt: 1284.062500

RSSI: -104

Got: Time: 14137521 Phase: 2 Arm: 1299.062500 Main: 1741.262451 Alt: 1284.500000

RSSI: -104

Got: Time: 14137688 Phase: 2 Arm: 1299.062500 Main: 1741.262451 Alt: 1284.250000

RSSI: -103

Got: Time: 14137854 Phase: 2 Arm: 1299.062500 Main: 1741.262451 Alt: 1284.125000

RSSI: -103

Got: Time: 14138021 Phase: 2 Arm: 1299.062500 Main: 1741.262451 Alt: 1284.062500

RSSI: -101

Got: Time: 14138188 Phase: 2 Arm: 1299.062500 Main: 1741.262451 Alt: 1284.187500

RSSI: -99

Got: Time: 14138355 Phase: 2 Arm: 1299.062500 Main: 1741.262451 Alt: 1283.937500

RSSI: -102

Got: Time: 14138521 Phase: 2 Arm: 1299.062500 Main: 1741.262451 Alt: 1284.062500

RSSI: -102

Got: Time: 14138688 Phase: 2 Arm: 1299.062500 Main: 1741.262451 Alt: 1283.750000

RSSI: -103

Got: Time: 14138855 Phase: 2 Arm: 1299.062500 Main: 1741.262451 Alt: 1284.375000

RSSI: -103

Got: Time: 14139022 Phase: 2 Arm: 1299.062500 Main: 1741.262451 Alt: 1283.937500

RSSI: -100

Got: Time: 14139188 Phase: 2 Arm: 1299.062500 Main: 1741.262451 Alt: 1284.062500

RSSI: -102

Got: Time: 14139355 Phase: 2 Arm: 1299.062500 Main: 1741.262451 Alt: 1283.750000

RSSI: -99

Got: Time: 14139522 Phase: 2 Arm: 1299.062500 Main: 1741.262451 Alt: 1284.250000

RSSI: -102

Got: Time: 14139689 Phase: 2 Arm: 1299.062500 Main: 1741.262451 Alt: 1284.687500

RSSI: -102

Got: Time: 14139856 Phase: 2 Arm: 1299.062500 Main: 1741.262451 Alt: 1284.250000

RSSI: -103

Got: Time: 14140022 Phase: 2 Arm: 1299.062500 Main: 1741.262451 Alt: 1284.187500

RSSI: -100

Got: Time: 14140189 Phase: 2 Arm: 1299.062500 Main: 1741.262451 Alt: 1284.187500

RSSI: -100

Got: Time: 14140356 Phase: 2 Arm: 1299.062500 Main: 1741.262451 Alt: 1283.625000

RSSI: -104

Got: Time: 14140523 Phase: 2 Arm: 1299.062500 Main: 1741.262451 Alt: 1284.000000

RSSI: -104

Got: Time: 14140689 Phase: 2 Arm: 1299.062500 Main: 1741.262451 Alt: 1283.937500

RSSI: -105

Got: Time: 14140856 Phase: 2 Arm: 1299.062500 Main: 1741.262451 Alt: 1283.937500

RSSI: -105

Got: Time: 14141023 Phase: 2 Arm: 1299.062500 Main: 1741.262451 Alt: 1284.312500

RSSI: -102

Got: Time: 14141190 Phase: 2 Arm: 1299.062500 Main: 1741.262451 Alt: 1283.812500

RSSI: -102

Got: Time: 14141356 Phase: 2 Arm: 1299.062500 Main: 1741.262451 Alt: 1284.062500

RSSI: -104

Got: Time: 14141523 Phase: 2 Arm: 1299.062500 Main: 1741.262451 Alt: 1284.312500

RSSI: -104

Got: Time: 14141690 Phase: 2 Arm: 1299.062500 Main: 1741.262451 Alt: 1284.187500

RSSI: -105

Got: Time: 14141857 Phase: 2 Arm: 1299.062500 Main: 1741.262451 Alt: 1284.625000

RSSI: -104

Got: Time: 14142024 Phase: 2 Arm: 1299.062500 Main: 1741.262451 Alt: 1283.750000

RSSI: -102

Got: Time: 14142190 Phase: 2 Arm: 1299.062500 Main: 1741.262451 Alt: 1284.375000

RSSI: -100

Got: Time: 14142357 Phase: 2 Arm: 1299.062500 Main: 1741.262451 Alt: 1284.500000

RSSI: -104

Got: Time: 14142524 Phase: 2 Arm: 1299.062500 Main: 1741.262451 Alt: 1284.500000

RSSI: -104

Got: Time: 14142691 Phase: 2 Arm: 1299.062500 Main: 1741.262451 Alt: 1284.125000

RSSI: -104

Got: Time: 14142857 Phase: 2 Arm: 1299.062500 Main: 1741.262451 Alt: 1283.937500

RSSI: -104

Got: Time: 14143024 Phase: 2 Arm: 1299.062500 Main: 1741.262451 Alt: 1284.125000

RSSI: -101

Got: Time: 14143191 Phase: 2 Arm: 1299.062500 Main: 1741.262451 Alt: 1283.562500

RSSI: -100

Got: Time: 14143358 Phase: 2 Arm: 1299.062500 Main: 1741.262451 Alt: 1284.250000

RSSI: -104

Got: Time: 14143524 Phase: 2 Arm: 1299.062500 Main: 1741.262451 Alt: 1284.375000

RSSI: -104

Got: Time: 14143691 Phase: 2 Arm: 1299.062500 Main: 1741.262451 Alt: 1284.187500

RSSI: -105

Got: Time: 14143858 Phase: 2 Arm: 1299.062500 Main: 1741.262451 Alt: 1284.125000

RSSI: -105

Got: Time: 14144025 Phase: 2 Arm: 1299.062500 Main: 1741.262451 Alt: 1284.187500

RSSI: -101

Got: Time: 14144191 Phase: 2 Arm: 1299.062500 Main: 1741.262451 Alt: 1284.250000

RSSI: -99

Got: Time: 14144358 Phase: 2 Arm: 1299.062500 Main: 1741.262451 Alt: 1284.437500

RSSI: -99

Got: Time: 14144525 Phase: 2 Arm: 1299.062500 Main: 1741.262451 Alt: 1284.500000

RSSI: -104

Got: Time: 14144692 Phase: 2 Arm: 1299.062500 Main: 1741.262451 Alt: 1283.750000

RSSI: -104

Got: Time: 14144859 Phase: 2 Arm: 1299.062500 Main: 1741.262451 Alt: 1284.250000

RSSI: -104

Got: Time: 14145025 Phase: 2 Arm: 1299.062500 Main: 1741.262451 Alt: 1284.187500

RSSI: -100

Got: Time: 14145192 Phase: 2 Arm: 1299.062500 Main: 1741.262451 Alt: 1284.437500

RSSI: -100

Got: Time: 14145359 Phase: 2 Arm: 1299.062500 Main: 1741.262451 Alt: 1284.062500

RSSI: -104

Got: Time: 14145526 Phase: 2 Arm: 1299.062500 Main: 1741.262451 Alt: 1283.937500

RSSI: -104

Got: Time: 14145692 Phase: 2 Arm: 1299.062500 Main: 1741.262451 Alt: 1284.437500

RSSI: -105

Got: Time: 14145859 Phase: 2 Arm: 1299.062500 Main: 1741.262451 Alt: 1284.312500

RSSI: -104

Got: Time: 14146026 Phase: 2 Arm: 1299.062500 Main: 1741.262451 Alt: 1284.562500

RSSI: -101

Got: Time: 14146193 Phase: 2 Arm: 1299.062500 Main: 1741.262451 Alt: 1284.250000

RSSI: -100

Got: Time: 14146359 Phase: 2 Arm: 1299.062500 Main: 1741.262451 Alt: 1283.812500

RSSI: -104

Got: Time: 14146526 Phase: 2 Arm: 1299.062500 Main: 1741.262451 Alt: 1284.437500

RSSI: -104

Got: Time: 14146693 Phase: 2 Arm: 1299.062500 Main: 1741.262451 Alt: 1283.750000

RSSI: -104

Got: Time: 14146860 Phase: 2 Arm: 1299.062500 Main: 1741.262451 Alt: 1284.562500

RSSI: -104

Got: Time: 14147027 Phase: 2 Arm: 1299.062500 Main: 1741.262451 Alt: 1283.937500

RSSI: -99

Got: Time: 14147193 Phase: 2 Arm: 1299.062500 Main: 1741.262451 Alt: 1284.187500

RSSI: -99

Got: Time: 14147360 Phase: 2 Arm: 1299.062500 Main: 1741.262451 Alt: 1284.187500

RSSI: -104

Got: Time: 14147527 Phase: 2 Arm: 1299.062500 Main: 1741.262451 Alt: 1283.875000

RSSI: -104

Got: Time: 14147694 Phase: 2 Arm: 1299.062500 Main: 1741.262451 Alt: 1284.187500

RSSI: -104

Got: Time: 14147860 Phase: 2 Arm: 1299.062500 Main: 1741.262451 Alt: 1284.375000

RSSI: -104

Got: Time: 14148027 Phase: 2 Arm: 1299.062500 Main: 1741.262451 Alt: 1283.937500

RSSI: -100

Got: Time: 14148194 Phase: 2 Arm: 1299.062500 Main: 1741.262451 Alt: 1284.562500

RSSI: -100

Got: Time: 14148361 Phase: 2 Arm: 1299.062500 Main: 1741.262451 Alt: 1284.125000

RSSI: -104

Got: Time: 14148527 Phase: 2 Arm: 1299.062500 Main: 1741.262451 Alt: 1284.375000

RSSI: -104

Got: Time: 14148694 Phase: 2 Arm: 1299.062500 Main: 1741.262451 Alt: 1283.937500

RSSI: -104

Got: Time: 14148861 Phase: 2 Arm: 1299.062500 Main: 1741.262451 Alt: 1284.125000

RSSI: -104

Got: Time: 14149028 Phase: 2 Arm: 1299.062500 Main: 1741.262451 Alt: 1284.562500

RSSI: -100

Got: Time: 14149195 Phase: 2 Arm: 1299.062500 Main: 1741.262451 Alt: 1284.437500

RSSI: -101

Got: Time: 14149361 Phase: 2 Arm: 1299.062500 Main: 1741.262451 Alt: 1284.125000

RSSI: -101

Got: Time: 14149528 Phase: 2 Arm: 1299.062500 Main: 1741.262451 Alt: 1284.375000

RSSI: -104

Got: Time: 14149695 Phase: 2 Arm: 1299.062500 Main: 1741.262451 Alt: 1284.250000

RSSI: -104

Got: Time: 14149862 Phase: 2 Arm: 1299.062500 Main: 1741.262451 Alt: 1284.312500

RSSI: -104

Got: Time: 14150028 Phase: 2 Arm: 1299.062500 Main: 1741.262451 Alt: 1284.562500

RSSI: -100

Got: Time: 14150195 Phase: 2 Arm: 1299.062500 Main: 1741.262451 Alt: 1284.250000

RSSI: -100

Got: Time: 14150362 Phase: 2 Arm: 1299.062500 Main: 1741.262451 Alt: 1284.312500

RSSI: -104

Got: Time: 14150529 Phase: 2 Arm: 1299.062500 Main: 1741.262451 Alt: 1284.187500

RSSI: -104

Got: Time: 14150695 Phase: 2 Arm: 1299.062500 Main: 1741.262451 Alt: 1283.937500

RSSI: -104

Got: Time: 14150862 Phase: 2 Arm: 1299.062500 Main: 1741.262451 Alt: 1284.187500

RSSI: -104

Got: Time: 14151029 Phase: 2 Arm: 1299.062500 Main: 1741.262451 Alt: 1283.937500

RSSI: -101

Got: Time: 14151196 Phase: 2 Arm: 1299.062500 Main: 1741.262451 Alt: 1283.937500

RSSI: -100

Got: Time: 14151363 Phase: 2 Arm: 1299.062500 Main: 1741.262451 Alt: 1283.875000

RSSI: -105

Got: Time: 14151529 Phase: 2 Arm: 1299.062500 Main: 1741.262451 Alt: 1283.437500

RSSI: -104

Got: Time: 14151696 Phase: 2 Arm: 1299.062500 Main: 1741.262451 Alt: 1284.250000

RSSI: -104

Got: Time: 14151863 Phase: 2 Arm: 1299.062500 Main: 1741.262451 Alt: 1284.062500

RSSI: -105

Got: Time: 14152030 Phase: 2 Arm: 1299.062500 Main: 1741.262451 Alt: 1283.875000

RSSI: -100

Got: Time: 14152196 Phase: 2 Arm: 1299.062500 Main: 1741.262451 Alt: 1284.375000

RSSI: -103

Got: Time: 14152363 Phase: 2 Arm: 1299.062500 Main: 1741.262451 Alt: 1284.812500

RSSI: -105

Got: Time: 14152530 Phase: 2 Arm: 1299.062500 Main: 1741.262451 Alt: 1284.187500

RSSI: -106

Got: Time: 14152697 Phase: 2 Arm: 1299.062500 Main: 1741.262451 Alt: 1284.250000

RSSI: -106

Got: Time: 14152863 Phase: 2 Arm: 1299.062500 Main: 1741.262451 Alt: 1284.187500

RSSI: -105

Got: Time: 14153030 Phase: 2 Arm: 1299.062500 Main: 1741.262451 Alt: 1283.937500

RSSI: -102

Got: Time: 14153197 Phase: 2 Arm: 1299.062500 Main: 1741.262451 Alt: 1284.312500

RSSI: -105

Got: Time: 14153364 Phase: 2 Arm: 1299.062500 Main: 1741.262451 Alt: 1284.312500

RSSI: -106

Got: Time: 14153530 Phase: 2 Arm: 1299.062500 Main: 1741.262451 Alt: 1284.062500

RSSI: -106

Got: Time: 14153697 Phase: 2 Arm: 1299.062500 Main: 1741.262451 Alt: 1284.625000

RSSI: -106

Got: Time: 14153864 Phase: 2 Arm: 1299.062500 Main: 1741.262451 Alt: 1284.062500

RSSI: -106

Got: Time: 14154031 Phase: 2 Arm: 1299.062500 Main: 1741.262451 Alt: 1284.125000

RSSI: -101

Got: Time: 14154198 Phase: 2 Arm: 1299.062500 Main: 1741.262451 Alt: 1284.625000

RSSI: -101

Got: Time: 14154364 Phase: 2 Arm: 1299.062500 Main: 1741.262451 Alt: 1284.375000

RSSI: -102

Got: Time: 14154531 Phase: 2 Arm: 1299.062500 Main: 1741.262451 Alt: 1283.937500

RSSI: -105

Got: Time: 14154698 Phase: 2 Arm: 1299.062500 Main: 1741.262451 Alt: 1284.125000

RSSI: -106

Got: Time: 14154865 Phase: 2 Arm: 1299.062500 Main: 1741.262451 Alt: 1284.062500

RSSI: -106

Got: Time: 14155031 Phase: 2 Arm: 1299.062500 Main: 1741.262451 Alt: 1284.187500

RSSI: -100

Got: Time: 14155198 Phase: 2 Arm: 1299.062500 Main: 1741.262451 Alt: 1284.375000

RSSI: -105

Got: Time: 14155365 Phase: 2 Arm: 1299.062500 Main: 1741.262451 Alt: 1284.187500

RSSI: -106

Got: Time: 14155532 Phase: 2 Arm: 1299.062500 Main: 1741.262451 Alt: 1284.250000

RSSI: -105

Got: Time: 14155698 Phase: 2 Arm: 1299.062500 Main: 1741.262451 Alt: 1284.500000

RSSI: -106

Got: Time: 14155865 Phase: 2 Arm: 1299.062500 Main: 1741.262451 Alt: 1284.187500

RSSI: -106

Got: Time: 14156032 Phase: 2 Arm: 1299.062500 Main: 1741.262451 Alt: 1284.562500

RSSI: -100

Got: Time: 14156199 Phase: 2 Arm: 1299.062500 Main: 1741.262451 Alt: 1284.500000

RSSI: -105

Got: Time: 14156366 Phase: 2 Arm: 1299.062500 Main: 1741.262451 Alt: 1284.562500

RSSI: -105

Got: Time: 14156532 Phase: 2 Arm: 1299.062500 Main: 1741.262451 Alt: 1284.500000

RSSI: -106

Got: Time: 14156699 Phase: 2 Arm: 1299.062500 Main: 1741.262451 Alt: 1283.937500

RSSI: -106

Got: Time: 14156866 Phase: 2 Arm: 1299.062500 Main: 1741.262451 Alt: 1284.062500

RSSI: -106

Got: Time: 14157033 Phase: 2 Arm: 1299.062500 Main: 1741.262451 Alt: 1284.375000

RSSI: -100

Got: Time: 14157199 Phase: 2 Arm: 1299.062500 Main: 1741.262451 Alt: 1284.500000

RSSI: -105

Got: Time: 14157366 Phase: 2 Arm: 1299.062500 Main: 1741.262451 Alt: 1284.187500

RSSI: -105

Got: Time: 14157533 Phase: 2 Arm: 1299.062500 Main: 1741.262451 Alt: 1284.312500

RSSI: -105

Got: Time: 14157700 Phase: 2 Arm: 1299.062500 Main: 1741.262451 Alt: 1284.500000

RSSI: -105

Got: Time: 14157866 Phase: 2 Arm: 1299.062500 Main: 1741.262451 Alt: 1284.000000

RSSI: -106

Got: Time: 14158033 Phase: 2 Arm: 1299.062500 Main: 1741.262451 Alt: 1284.625000

RSSI: -103

Got: Time: 14158200 Phase: 2 Arm: 1299.062500 Main: 1741.262451 Alt: 1284.062500

RSSI: -103

Got: Time: 14158367 Phase: 2 Arm: 1299.062500 Main: 1741.262451 Alt: 1284.125000

RSSI: -106

Got: Time: 14158534 Phase: 2 Arm: 1299.062500 Main: 1741.262451 Alt: 1284.562500

RSSI: -106

Got: Time: 14158700 Phase: 2 Arm: 1299.062500 Main: 1741.262451 Alt: 1284.312500

RSSI: -106

Got: Time: 14158867 Phase: 2 Arm: 1299.062500 Main: 1741.262451 Alt: 1284.687500

RSSI: -106

Got: Time: 14159034 Phase: 2 Arm: 1299.062500 Main: 1741.262451 Alt: 1284.437500

RSSI: -102

Got: Time: 14159201 Phase: 2 Arm: 1299.062500 Main: 1741.262451 Alt: 1284.187500

RSSI: -102

Got: Time: 14159367 Phase: 2 Arm: 1299.062500 Main: 1741.262451 Alt: 1284.062500

RSSI: -102

Got: Time: 14159534 Phase: 2 Arm: 1299.062500 Main: 1741.262451 Alt: 1284.187500

RSSI: -106

Got: Time: 14159701 Phase: 2 Arm: 1299.062500 Main: 1741.262451 Alt: 1283.875000

RSSI: -106

Got: Time: 14159868 Phase: 2 Arm: 1299.062500 Main: 1741.262451 Alt: 1284.750000

RSSI: -106

Got: Time: 14160034 Phase: 2 Arm: 1299.062500 Main: 1741.262451 Alt: 1284.562500

RSSI: -102

Got: Time: 14160201 Phase: 2 Arm: 1299.062500 Main: 1741.262451 Alt: 1284.312500

RSSI: -103

Got: Time: 14160368 Phase: 2 Arm: 1299.062500 Main: 1741.262451 Alt: 1284.187500

RSSI: -106

Got: Time: 14160535 Phase: 2 Arm: 1299.062500 Main: 1741.262451 Alt: 1284.437500

RSSI: -106

Got: Time: 14160701 Phase: 2 Arm: 1299.062500 Main: 1741.262451 Alt: 1284.250000

RSSI: -106

Got: Time: 14160868 Phase: 2 Arm: 1299.062500 Main: 1741.262451 Alt: 1284.375000

RSSI: -106

Got: Time: 14161035 Phase: 2 Arm: 1299.062500 Main: 1741.262451 Alt: 1284.500000

RSSI: -104

Got: Time: 14161202 Phase: 2 Arm: 1299.062500 Main: 1741.262451 Alt: 1284.375000

RSSI: -106

Got: Time: 14161369 Phase: 2 Arm: 1299.062500 Main: 1741.262451 Alt: 1284.062500

RSSI: -106

Got: Time: 14161535 Phase: 2 Arm: 1299.062500 Main: 1741.262451 Alt: 1284.500000

RSSI: -107

Got: Time: 14161702 Phase: 2 Arm: 1299.062500 Main: 1741.262451 Alt: 1284.375000

RSSI: -106

Got: Time: 14161869 Phase: 2 Arm: 1299.062500 Main: 1741.262451 Alt: 1284.312500

RSSI: -106

Got: Time: 14162036 Phase: 2 Arm: 1299.062500 Main: 1741.262451 Alt: 1284.500000

RSSI: -104

Got: Time: 14162202 Phase: 2 Arm: 1299.062500 Main: 1741.262451 Alt: 1284.562500

RSSI: -105

Got: Time: 14162369 Phase: 2 Arm: 1299.062500 Main: 1741.262451 Alt: 1284.875000

RSSI: -106

Got: Time: 14162536 Phase: 2 Arm: 1299.062500 Main: 1741.262451 Alt: 1284.187500

RSSI: -106

Got: Time: 14162703 Phase: 2 Arm: 1299.062500 Main: 1741.262451 Alt: 1284.500000

RSSI: -106

Got: Time: 14162869 Phase: 2 Arm: 1299.062500 Main: 1741.262451 Alt: 1284.375000

RSSI: -106

Got: Time: 14163036 Phase: 2 Arm: 1299.062500 Main: 1741.262451 Alt: 1284.000000

RSSI: -103

Got: Time: 14163203 Phase: 2 Arm: 1299.062500 Main: 1741.262451 Alt: 1284.125000

RSSI: -105

Got: Time: 14163370 Phase: 2 Arm: 1299.062500 Main: 1741.262451 Alt: 1284.562500

RSSI: -106

Got: Time: 14163537 Phase: 2 Arm: 1299.062500 Main: 1741.262451 Alt: 1284.187500

RSSI: -106

Got: Time: 14163703 Phase: 2 Arm: 1299.062500 Main: 1741.262451 Alt: 1284.312500

RSSI: -106

Got: Time: 14163870 Phase: 2 Arm: 1299.062500 Main: 1741.262451 Alt: 1283.937500

RSSI: -107

Got: Time: 14164037 Phase: 2 Arm: 1299.062500 Main: 1741.262451 Alt: 1284.187500

RSSI: -102

Got: Time: 14164204 Phase: 2 Arm: 1299.062500 Main: 1741.262451 Alt: 1284.187500

RSSI: -104

Got: Time: 14164370 Phase: 2 Arm: 1299.062500 Main: 1741.262451 Alt: 1284.062500

RSSI: -103

Got: Time: 14164537 Phase: 2 Arm: 1299.062500 Main: 1741.262451 Alt: 1284.187500

RSSI: -106

Got: Time: 14164704 Phase: 2 Arm: 1299.062500 Main: 1741.262451 Alt: 1284.375000

RSSI: -106

Got: Time: 14164871 Phase: 2 Arm: 1299.062500 Main: 1741.262451 Alt: 1283.937500

RSSI: -106

Got: Time: 14165037 Phase: 2 Arm: 1299.062500 Main: 1741.262451 Alt: 1284.562500

RSSI: -103

Got: Time: 14165204 Phase: 2 Arm: 1299.062500 Main: 1741.262451 Alt: 1284.437500

RSSI: -104

Got: Time: 14165371 Phase: 2 Arm: 1299.062500 Main: 1741.262451 Alt: 1284.375000

RSSI: -106

Got: Time: 14165538 Phase: 2 Arm: 1299.062500 Main: 1741.262451 Alt: 1284.000000

RSSI: -106

Got: Time: 14165705 Phase: 2 Arm: 1299.062500 Main: 1741.262451 Alt: 1283.937500

RSSI: -106

Got: Time: 14165871 Phase: 2 Arm: 1299.062500 Main: 1741.262451 Alt: 1284.812500

RSSI: -107

Got: Time: 14166038 Phase: 2 Arm: 1299.062500 Main: 1741.262451 Alt: 1284.062500

RSSI: -104

Got: Time: 14166205 Phase: 2 Arm: 1299.062500 Main: 1741.262451 Alt: 1284.062500

RSSI: -102

Got: Time: 14166372 Phase: 2 Arm: 1299.062500 Main: 1741.262451 Alt: 1284.562500

RSSI: -107

Got: Time: 14166538 Phase: 2 Arm: 1299.062500 Main: 1741.262451 Alt: 1284.562500

RSSI: -106

Got: Time: 14166705 Phase: 2 Arm: 1299.062500 Main: 1741.262451 Alt: 1284.937500

RSSI: -106

Got: Time: 14166872 Phase: 2 Arm: 1299.062500 Main: 1741.262451 Alt: 1284.000000

RSSI: -107

Got: Time: 14167039 Phase: 2 Arm: 1299.062500 Main: 1741.262451 Alt: 1284.312500

RSSI: -104

Got: Time: 14167205 Phase: 2 Arm: 1299.062500 Main: 1741.262451 Alt: 1283.937500

RSSI: -103

Got: Time: 14167372 Phase: 2 Arm: 1299.062500 Main: 1741.262451 Alt: 1284.312500

RSSI: -106

Got: Time: 14167539 Phase: 2 Arm: 1299.062500 Main: 1741.262451 Alt: 1284.375000

RSSI: -107

Got: Time: 14167706 Phase: 2 Arm: 1299.062500 Main: 1741.262451 Alt: 1284.375000

RSSI: -106

Got: Time: 14167872 Phase: 2 Arm: 1299.062500 Main: 1741.262451 Alt: 1284.687500

RSSI: -107

Got: Time: 14168039 Phase: 2 Arm: 1299.062500 Main: 1741.262451 Alt: 1284.562500

RSSI: -102

Got: Time: 14168206 Phase: 2 Arm: 1299.062500 Main: 1741.262451 Alt: 1284.312500

RSSI: -102

Got: Time: 14168373 Phase: 2 Arm: 1299.062500 Main: 1741.262451 Alt: 1284.500000

RSSI: -106

Got: Time: 14168540 Phase: 2 Arm: 1299.062500 Main: 1741.262451 Alt: 1283.875000

RSSI: -106

Got: Time: 14168706 Phase: 2 Arm: 1299.062500 Main: 1741.262451 Alt: 1284.000000

RSSI: -106

Got: Time: 14168873 Phase: 2 Arm: 1299.062500 Main: 1741.262451 Alt: 1284.562500

RSSI: -106

Got: Time: 14169040 Phase: 2 Arm: 1299.062500 Main: 1741.262451 Alt: 1284.187500

RSSI: -105

Got: Time: 14169207 Phase: 2 Arm: 1299.062500 Main: 1741.262451 Alt: 1284.125000

RSSI: -102

Got: Time: 14169373 Phase: 2 Arm: 1299.062500 Main: 1741.262451 Alt: 1284.125000

RSSI: -102

Got: Time: 14169540 Phase: 2 Arm: 1299.062500 Main: 1741.262451 Alt: 1284.500000

RSSI: -106

Got: Time: 14169707 Phase: 2 Arm: 1299.062500 Main: 1741.262451 Alt: 1284.375000

RSSI: -107

Got: Time: 14169874 Phase: 2 Arm: 1299.062500 Main: 1741.262451 Alt: 1284.812500

RSSI: -107

Got: Time: 14170040 Phase: 2 Arm: 1299.062500 Main: 1741.262451 Alt: 1284.437500

RSSI: -102

Got: Time: 14170207 Phase: 2 Arm: 1299.062500 Main: 1741.262451 Alt: 1284.687500

RSSI: -102

Got: Time: 14170374 Phase: 2 Arm: 1299.062500 Main: 1741.262451 Alt: 1284.125000

RSSI: -106

Got: Time: 14170541 Phase: 2 Arm: 1299.062500 Main: 1741.262451 Alt: 1284.562500

RSSI: -107

Got: Time: 14170708 Phase: 2 Arm: 1299.062500 Main: 1741.262451 Alt: 1284.750000

RSSI: -107

Got: Time: 14170874 Phase: 2 Arm: 1299.062500 Main: 1741.262451 Alt: 1284.687500

RSSI: -106

Got: Time: 14171041 Phase: 2 Arm: 1299.062500 Main: 1741.262451 Alt: 1284.250000

RSSI: -101

Got: Time: 14171208 Phase: 2 Arm: 1299.062500 Main: 1741.262451 Alt: 1284.375000

RSSI: -106

Got: Time: 14171375 Phase: 2 Arm: 1299.062500 Main: 1741.262451 Alt: 1283.937500

RSSI: -107

Got: Time: 14171541 Phase: 2 Arm: 1299.062500 Main: 1741.262451 Alt: 1284.125000

RSSI: -107

Got: Time: 14171708 Phase: 2 Arm: 1299.062500 Main: 1741.262451 Alt: 1284.437500

RSSI: -107

Got: Time: 14171875 Phase: 2 Arm: 1299.062500 Main: 1741.262451 Alt: 1284.187500

RSSI: -107

Got: Time: 14172042 Phase: 2 Arm: 1299.062500 Main: 1741.262451 Alt: 1284.375000

RSSI: -105

Got: Time: 14172208 Phase: 2 Arm: 1299.062500 Main: 1741.262451 Alt: 1284.500000

RSSI: -102

Got: Time: 14172375 Phase: 2 Arm: 1299.062500 Main: 1741.262451 Alt: 1283.937500

RSSI: -106

Got: Time: 14172542 Phase: 2 Arm: 1299.062500 Main: 1741.262451 Alt: 1284.125000

RSSI: -106

Got: Time: 14172709 Phase: 2 Arm: 1299.062500 Main: 1741.262451 Alt: 1284.437500

RSSI: -107

Got: Time: 14172876 Phase: 2 Arm: 1299.062500 Main: 1741.262451 Alt: 1284.437500

RSSI: -107

Got: Time: 14173042 Phase: 2 Arm: 1299.062500 Main: 1741.262451 Alt: 1284.562500

RSSI: -103

Got: Time: 14173209 Phase: 2 Arm: 1299.062500 Main: 1741.262451 Alt: 1283.875000

RSSI: -103

Got: Time: 14173376 Phase: 2 Arm: 1299.062500 Main: 1741.262451 Alt: 1284.375000

RSSI: -107

Got: Time: 14173543 Phase: 2 Arm: 1299.062500 Main: 1741.262451 Alt: 1284.625000

RSSI: -106

Got: Time: 14173709 Phase: 2 Arm: 1299.062500 Main: 1741.262451 Alt: 1283.937500

RSSI: -106

Got: Time: 14173876 Phase: 2 Arm: 1299.062500 Main: 1741.262451 Alt: 1284.812500

RSSI: -107

Got: Time: 14174043 Phase: 2 Arm: 1299.062500 Main: 1741.262451 Alt: 1284.562500

RSSI: -103

Got: Time: 14174210 Phase: 2 Arm: 1299.062500 Main: 1741.262451 Alt: 1284.062500

RSSI: -102

Got: Time: 14174376 Phase: 2 Arm: 1299.062500 Main: 1741.262451 Alt: 1284.000000

RSSI: -102

Got: Time: 14174543 Phase: 2 Arm: 1299.062500 Main: 1741.262451 Alt: 1284.312500

RSSI: -107

Got: Time: 14174710 Phase: 2 Arm: 1299.062500 Main: 1741.262451 Alt: 1284.375000

RSSI: -106

Got: Time: 14174877 Phase: 2 Arm: 1299.062500 Main: 1741.262451 Alt: 1284.375000

RSSI: -106

Got: Time: 14175043 Phase: 2 Arm: 1299.062500 Main: 1741.262451 Alt: 1284.187500

RSSI: -103

Got: Time: 14175210 Phase: 2 Arm: 1299.062500 Main: 1741.262451 Alt: 1284.187500

RSSI: -103

Got: Time: 14175377 Phase: 2 Arm: 1299.062500 Main: 1741.262451 Alt: 1284.562500

RSSI: -107

Got: Time: 14175544 Phase: 2 Arm: 1299.062500 Main: 1741.262451 Alt: 1284.250000

RSSI: -106

Got: Time: 14175711 Phase: 2 Arm: 1299.062500 Main: 1741.262451 Alt: 1283.875000

RSSI: -106

Got: Time: 14175877 Phase: 2 Arm: 1299.062500 Main: 1741.262451 Alt: 1284.687500

RSSI: -107

Got: Time: 14176044 Phase: 2 Arm: 1299.062500 Main: 1741.262451 Alt: 1284.062500

RSSI: -104

Got: Time: 14176211 Phase: 2 Arm: 1299.062500 Main: 1741.262451 Alt: 1284.125000

RSSI: -103

Got: Time: 14176378 Phase: 2 Arm: 1299.062500 Main: 1741.262451 Alt: 1284.125000

RSSI: -106

Got: Time: 14176544 Phase: 2 Arm: 1299.062500 Main: 1741.262451 Alt: 1284.062500

RSSI: -107

Got: Time: 14176711 Phase: 2 Arm: 1299.062500 Main: 1741.262451 Alt: 1284.375000

RSSI: -107

Got: Time: 14176878 Phase: 2 Arm: 1299.062500 Main: 1741.262451 Alt: 1283.500000

RSSI: -106

Got: Time: 14177045 Phase: 2 Arm: 1299.062500 Main: 1741.262451 Alt: 1283.937500

RSSI: -104

Got: Time: 14177211 Phase: 2 Arm: 1299.062500 Main: 1741.262451 Alt: 1284.500000

RSSI: -104

Got: Time: 14177378 Phase: 2 Arm: 1299.062500 Main: 1741.262451 Alt: 1284.812500

RSSI: -106

Got: Time: 14177545 Phase: 2 Arm: 1299.062500 Main: 1741.262451 Alt: 1284.125000

RSSI: -107

Got: Time: 14177712 Phase: 2 Arm: 1299.062500 Main: 1741.262451 Alt: 1284.437500

RSSI: -106

Got: Time: 14177879 Phase: 2 Arm: 1299.062500 Main: 1741.262451 Alt: 1284.000000

RSSI: -107

Got: Time: 14178045 Phase: 2 Arm: 1299.062500 Main: 1741.262451 Alt: 1284.187500

RSSI: -104

Got: Time: 14178212 Phase: 2 Arm: 1299.062500 Main: 1741.262451 Alt: 1284.375000

RSSI: -103

Got: Time: 14178379 Phase: 2 Arm: 1299.062500 Main: 1741.262451 Alt: 1284.875000

RSSI: -107

Got: Time: 14178546 Phase: 2 Arm: 1299.062500 Main: 1741.262451 Alt: 1284.312500

RSSI: -106

Got: Time: 14178712 Phase: 2 Arm: 1299.062500 Main: 1741.262451 Alt: 1283.812500

RSSI: -107

Got: Time: 14178879 Phase: 2 Arm: 1299.062500 Main: 1741.262451 Alt: 1284.500000

RSSI: -106

Got: Time: 14179046 Phase: 2 Arm: 1299.062500 Main: 1741.262451 Alt: 1284.812500

RSSI: -103

Got: Time: 14179213 Phase: 2 Arm: 1299.062500 Main: 1741.262451 Alt: 1283.937500

RSSI: -104

Got: Time: 14179379 Phase: 2 Arm: 1299.062500 Main: 1741.262451 Alt: 1284.500000

RSSI: -103

Got: Time: 14179546 Phase: 2 Arm: 1299.062500 Main: 1741.262451 Alt: 1283.687500

RSSI: -107

Got: Time: 14179713 Phase: 2 Arm: 1299.062500 Main: 1741.262451 Alt: 1284.125000

RSSI: -107

Got: Time: 14179880 Phase: 2 Arm: 1299.062500 Main: 1741.262451 Alt: 1284.937500

RSSI: -107

Got: Time: 14180047 Phase: 2 Arm: 1299.062500 Main: 1741.262451 Alt: 1283.750000

RSSI: -104

Got: Time: 14180213 Phase: 2 Arm: 1299.062500 Main: 1741.262451 Alt: 1284.187500

RSSI: -104

Got: Time: 14180380 Phase: 2 Arm: 1299.062500 Main: 1741.262451 Alt: 1284.062500

RSSI: -106

Got: Time: 14180547 Phase: 2 Arm: 1299.062500 Main: 1741.262451 Alt: 1284.562500

RSSI: -107

Got: Time: 14180714 Phase: 2 Arm: 1299.062500 Main: 1741.262451 Alt: 1284.375000

RSSI: -109

Got: Time: 14180880 Phase: 2 Arm: 1299.062500 Main: 1741.262451 Alt: 1284.625000

RSSI: -102

Got: Time: 14181047 Phase: 2 Arm: 1299.062500 Main: 1741.262451 Alt: 1285.625000

RSSI: -99

Got: Time: 14181214 Phase: 2 Arm: 1299.062500 Main: 1741.262451 Alt: 1288.750000

RSSI: -95

Got: Time: 14181381 Phase: 2 Arm: 1299.062500 Main: 1741.262451 Alt: 1296.500000

RSSI: -98

Got: Time: 14181381 Phase: 3 alt: 1308.000000

RSSI: -104

Got: Time: 14181716 Phase: 3 alt: 1323.687500

RSSI: -96

Got: Time: 14181885 Phase: 3 alt: 1341.312500

RSSI: -97

Got: Time: 14182055 Phase: 3 alt: 1361.750000

RSSI: -97

Got: Time: 14182225 Phase: 3 alt: 1383.375000

RSSI: -92

Got: Time: 14182394 Phase: 3 alt: 1415.125000

RSSI: -93

Got: Time: 14182565 Phase: 3 alt: 1443.687500

RSSI: -96

Got: Time: 14182733 Phase: 3 alt: 1477.812500

RSSI: -96

Got: Time: 14182904 Phase: 3 alt: 1509.125000

RSSI: -92

Got: Time: 14183075 Phase: 3 alt: 1544.750000

RSSI: -91

Got: Time: 14183244 Phase: 3 alt: 1569.625000

RSSI: -90

Got: Time: 14183414 Phase: 3 alt: 1615.812500

RSSI: -93

Got: Time: 14183583 Phase: 3 alt: 1651.312500

RSSI: -96

Got: Time: 14183753 Phase: 3 alt: 1687.562500

RSSI: -96

Got: Time: 14183922 Phase: 3 alt: 1724.562500

RSSI: -96

Got: Time: 14184091 Phase: 3 alt: 1759.562500

RSSI: -95

Got: Time: 14184260 Phase: 3 alt: 1785.812500

RSSI: -90

Got: Time: 14184430 Phase: 3 alt: 1828.500000

RSSI: -90

Got: Time: 14184598 Phase: 3 alt: 1867.500000

RSSI: -90

Got: Time: 14184769 Phase: 3 alt: 1907.812500

RSSI: -90

Got: Time: 14184938 Phase: 3 alt: 1945.375000

RSSI: -90

Got: Time: 14185108 Phase: 3 alt: 1980.687500

RSSI: -89

Got: Time: 14185279 Phase: 3 alt: 2001.187500

RSSI: -92

Got: Time: 14185448 Phase: 3 alt: 2043.875000

RSSI: -91

Got: Time: 14185619 Phase: 3 alt: 2074.437500

RSSI: -92

Got: Time: 14185787 Phase: 3 alt: 2105.875000

RSSI: -92

Got: Time: 14185958 Phase: 3 alt: 2134.812500

RSSI: -93

Got: Time: 14186128 Phase: 3 alt: 2165.375000

RSSI: -92

Got: Time: 14186297 Phase: 3 alt: 2192.000000

RSSI: -95

Got: Time: 14186465 Phase: 3 alt: 2220.875000

RSSI: -95

Got: Time: 14186634 Phase: 3 alt: 2246.625000

RSSI: -93

Got: Time: 14186803 Phase: 3 alt: 2272.062500

RSSI: -95

Got: Time: 14186973 Phase: 3 alt: 2298.500000

RSSI: -96

Got: Time: 14187142 Phase: 3 alt: 2325.187500

RSSI: -95

Got: Time: 14187313 Phase: 3 alt: 2350.687500

RSSI: -98

Got: Time: 14187484 Phase: 3 alt: 2376.312500

RSSI: -100

Got: Time: 14187653 Phase: 3 alt: 2401.125000

RSSI: -101

Got: Time: 14187823 Phase: 3 alt: 2426.125000

RSSI: -101

Got: Time: 14187992 Phase: 3 alt: 2448.937500

RSSI: -99

Got: Time: 14188163 Phase: 3 alt: 2472.875000

RSSI: -92

Got: Time: 14188502 Phase: 3 alt: 2521.375000

RSSI: -96

Got: Time: 14188673 Phase: 3 alt: 2541.625000

RSSI: -95

Got: Time: 14188841 Phase: 3 alt: 2566.312500

RSSI: -96

Got: Time: 14189010 Phase: 3 alt: 2587.437500

RSSI: -96

Got: Time: 14189179 Phase: 3 alt: 2607.750000

RSSI: -92

Got: Time: 14189347 Phase: 3 alt: 2629.687500

RSSI: -92

Got: Time: 14189518 Phase: 3 alt: 2649.375000

RSSI: -95

Got: Time: 14189688 Phase: 3 alt: 2668.812500

RSSI: -95

Got: Time: 14189857 Phase: 3 alt: 2689.437500

RSSI: -96

Got: Time: 14190028 Phase: 3 alt: 2710.250000

RSSI: -92

Got: Time: 14190196 Phase: 3 alt: 2728.625000

RSSI: -93

Got: Time: 14190367 Phase: 3 alt: 2750.000000

RSSI: -96

Got: Time: 14190538 Phase: 3 alt: 2769.625000

RSSI: -96

Got: Time: 14190707 Phase: 3 alt: 2786.937500

RSSI: -97

Got: Time: 14190877 Phase: 3 alt: 2808.250000

RSSI: -97

Got: Time: 14191046 Phase: 3 alt: 2825.062500

RSSI: -95

Got: Time: 14191216 Phase: 3 alt: 2839.937500

RSSI: -96

Got: Time: 14191386 Phase: 3 alt: 2859.937500

RSSI: -99

Got: Time: 14191555 Phase: 3 alt: 2876.000000

RSSI: -99

Got: Time: 14191723 Phase: 3 alt: 2893.000000

RSSI: -100

Got: Time: 14191893 Phase: 3 alt: 2910.062500

RSSI: -100

Got: Time: 14192062 Phase: 3 alt: 2925.562500

RSSI: -98

Got: Time: 14192232 Phase: 3 alt: 2941.500000

RSSI: -99

Got: Time: 14192401 Phase: 3 alt: 2958.750000

RSSI: -102

Got: Time: 14192572 Phase: 3 alt: 2973.875000

RSSI: -102

Got: Time: 14192743 Phase: 3 alt: 2987.562500

RSSI: -102

Got: Time: 14192911 Phase: 3 alt: 3001.625000

RSSI: -103

Got: Time: 14193082 Phase: 3 alt: 3016.250000

RSSI: -103

Got: Time: 14193251 Phase: 3 alt: 3025.125000

RSSI: -103

Got: Time: 14193421 Phase: 3 alt: 3043.312500

RSSI: -106

Got: Time: 14193592 Phase: 3 alt: 3055.500000

RSSI: -106

Got: Time: 14193761 Phase: 3 alt: 3068.812500

RSSI: -105

Got: Time: 14193931 Phase: 3 alt: 3083.562500

RSSI: -104

Got: Time: 14194100 Phase: 3 alt: 3095.812500

RSSI: -102

Got: Time: 14194268 Phase: 3 alt: 3107.500000

RSSI: -103

Got: Time: 14194437 Phase: 3 alt: 3118.687500

RSSI: -101

Got: Time: 14194606 Phase: 3 alt: 3130.000000

RSSI: -105

Got: Time: 14194776 Phase: 3 alt: 3141.562500

RSSI: -105

Got: Time: 14194947 Phase: 3 alt: 3151.312500

RSSI: -104

Got: Time: 14195116 Phase: 3 alt: 3163.125000

RSSI: -104

Got: Time: 14195286 Phase: 3 alt: 3172.437500

RSSI: -104

Got: Time: 14195455 Phase: 3 alt: 3185.187500

RSSI: -104

Got: Time: 14195626 Phase: 3 alt: 3194.437500

RSSI: -104

Got: Time: 14195796 Phase: 3 alt: 3204.875000

RSSI: -103

Got: Time: 14195965 Phase: 3 alt: 3213.750000

RSSI: -104

Got: Time: 14196136 Phase: 3 alt: 3223.062500

RSSI: -100

Got: Time: 14196304 Phase: 3 alt: 3231.750000

RSSI: -103

Got: Time: 14196474 Phase: 3 alt: 3239.187500

RSSI: -103

Got: Time: 14196642 Phase: 3 alt: 3248.062500

RSSI: -103

Got: Time: 14196811 Phase: 3 alt: 3255.250000

RSSI: -102

Got: Time: 14196981 Phase: 3 alt: 3263.687500

RSSI: -101

Got: Time: 14197151 Phase: 3 alt: 3272.812500

RSSI: -99

Got: Time: 14197320 Phase: 3 alt: 3279.875000

RSSI: -101

Got: Time: 14197490 Phase: 3 alt: 3286.812500

RSSI: -101

Got: Time: 14197659 Phase: 3 alt: 3293.375000

RSSI: -101

Got: Time: 14197830 Phase: 3 alt: 3299.750000

RSSI: -100

Got: Time: 14198001 Phase: 3 alt: 3305.687500

RSSI: -100

Got: Time: 14198169 Phase: 3 alt: 3311.250000

RSSI: -99

Got: Time: 14198340 Phase: 3 alt: 3316.312500

RSSI: -101

Got: Time: 14198509 Phase: 3 alt: 3322.187500

RSSI: -101

Got: Time: 14198678 Phase: 3 alt: 3326.937500

RSSI: -102

Got: Time: 14198847 Phase: 3 alt: 3332.625000

RSSI: -102

Got: Time: 14199015 Phase: 3 alt: 3338.937500

RSSI: -103

Got: Time: 14199185 Phase: 3 alt: 3343.500000

RSSI: -102

Got: Time: 14199355 Phase: 3 alt: 3347.562500

RSSI: -104

Got: Time: 14199523 Phase: 3 alt: 3351.687500

RSSI: -111

Got: Time: 14199694 Phase: 3 alt: 3355.500000

RSSI: -111

Got: Time: 14199863 Phase: 3 alt: 3358.625000

RSSI: -108

Got: Time: 14200034 Phase: 3 alt: 3362.250000

RSSI: -100

Got: Time: 14201256 Phase: 4 alt: 3380.187500

RSSI: -104

Got: Time: 14201425 Phase: 4 alt: 3381.562500

RSSI: -108

Got: Time: 14201596 Phase: 4 alt: 3382.000000

RSSI: -107

Got: Time: 14201764 Phase: 4 alt: 3383.000000

RSSI: -107

Got: Time: 14201934 Phase: 4 alt: 3382.625000

RSSI: -106

Got: Time: 14202104 Phase: 4 alt: 3382.750000

RSSI: -105

Got: Time: 14202272 Phase: 4 alt: 3382.625000

RSSI: -115

Got: Time: 14202441 Phase: 4 alt: 3371.250000

RSSI: -114

Got: Time: 14202611 Phase: 4 alt: 3381.687500

RSSI: -109

Got: Time: 14202780 Phase: 4 alt: 3381.312500

RSSI: -119

Got: Time: 14202950 Phase: 4 alt: 3381.062500

RSSI: -129

Got: Time: 14203119 Phase: 4 alt: 3381.437500

RSSI: -108

Got: Time: 14203290 Phase: 4 alt: 3379.937500

RSSI: -113

Got: Time: 14203461 Phase: 4 alt: 3379.125000

RSSI: -114

Got: Time: 14203800 Phase: 4 alt: 3377.187500

RSSI: -103

Got: Time: 14203969 Phase: 4 alt: 3375.375000

RSSI: -102

Got: Time: 14204139 Phase: 4 alt: 3375.250000

RSSI: -100

Got: Time: 14204309 Phase: 4 alt: 3381.000000

RSSI: -95

Got: Time: 14204478 Phase: 4 alt: 3385.062500

RSSI: -96

Got: Time: 14204646 Phase: 4 alt: 3372.125000

RSSI: -101

Got: Time: 14204815 Phase: 4 alt: 3365.625000

RSSI: -106

Got: Time: 14204985 Phase: 4 alt: 3366.125000

RSSI: -104

Got: Time: 14205154 Phase: 4 alt: 3359.687500

RSSI: -102

Got: Time: 14205494 Phase: 4 alt: 3353.750000

RSSI: -107

Got: Time: 14205665 Phase: 4 alt: 3346.562500

RSSI: -104

Got: Time: 14205834 Phase: 4 alt: 3345.625000

RSSI: -102

Got: Time: 14206004 Phase: 4 alt: 3339.125000

RSSI: -106

Got: Time: 14206344 Phase: 4 alt: 3328.562500

RSSI: -105

Got: Time: 14206514 Phase: 4 alt: 3339.500000

RSSI: -114

Got: Time: 14206683 Phase: 4 alt: 3327.375000

RSSI: -112

Got: Time: 14206853 Phase: 4 alt: 3314.312500

RSSI: -96

Got: Time: 14207022 Phase: 4 alt: 3330.625000

RSSI: -92

Got: Time: 14207191 Phase: 4 alt: 3318.687500

RSSI: -95

Got: Time: 14207359 Phase: 4 alt: 3320.937500

RSSI: -102

Got: Time: 14207528 Phase: 4 alt: 3314.500000

RSSI: -102

Got: Time: 14207699 Phase: 4 alt: 3308.312500

RSSI: -113

Got: Time: 14207869 Phase: 4 alt: 3303.187500

RSSI: -101

Got: Time: 14208038 Phase: 4 alt: 3293.250000

RSSI: -100

Got: Time: 14208209 Phase: 4 alt: 3287.125000

RSSI: -98

Got: Time: 14208377 Phase: 4 alt: 3288.687500

RSSI: -102

Got: Time: 14208548 Phase: 4 alt: 3285.250000

RSSI: -105

Got: Time: 14208719 Phase: 4 alt: 3286.750000

RSSI: -100

Got: Time: 14208888 Phase: 4 alt: 3280.375000

RSSI: -101

Got: Time: 14209058 Phase: 4 alt: 3277.062500

RSSI: -95

Got: Time: 14209227 Phase: 4 alt: 3271.500000

RSSI: -99

Got: Time: 14209396 Phase: 4 alt: 3260.375000

RSSI: -97

Got: Time: 14209565 Phase: 4 alt: 3256.062500

RSSI: -102

Got: Time: 14209734 Phase: 4 alt: 3270.312500

RSSI: -104

Got: Time: 14209903 Phase: 4 alt: 3256.562500

RSSI: -103

Got: Time: 14210073 Phase: 4 alt: 3248.812500

RSSI: -99

Got: Time: 14210413 Phase: 4 alt: 3247.000000

RSSI: -116

Got: Time: 14210581 Phase: 4 alt: 3248.937500

RSSI: -106

Got: Time: 14210752 Phase: 4 alt: 3245.187500

RSSI: -99

Got: Time: 14210923 Phase: 4 alt: 3229.562500

RSSI: -97

Got: Time: 14211092 Phase: 4 alt: 3220.750000

RSSI: -103

Got: Time: 14211262 Phase: 4 alt: 3223.062500

RSSI: -105

Got: Time: 14211431 Phase: 4 alt: 3223.562500

RSSI: -102

Got: Time: 14211601 Phase: 4 alt: 3224.375000

RSSI: -112

Got: Time: 14211770 Phase: 4 alt: 3217.625000

RSSI: -95

Got: Time: 14211939 Phase: 4 alt: 3213.687500

RSSI: -107

Got: Time: 14212277 Phase: 4 alt: 3197.187500

RSSI: -106

Got: Time: 14212447 Phase: 4 alt: 3188.312500

RSSI: -100

Got: Time: 14212617 Phase: 4 alt: 3179.062500

RSSI: -103

Got: Time: 14212786 Phase: 4 alt: 3175.000000

RSSI: -96

Got: Time: 14212956 Phase: 4 alt: 3167.875000

RSSI: -101

Got: Time: 14213127 Phase: 4 alt: 3168.750000

RSSI: -97

Got: Time: 14213296 Phase: 4 alt: 3174.187500

RSSI: -106

Got: Time: 14213466 Phase: 4 alt: 3170.062500

RSSI: -97

Got: Time: 14213635 Phase: 4 alt: 3151.437500

RSSI: -108

Got: Time: 14213805 Phase: 4 alt: 3153.500000

RSSI: -105

Got: Time: 14213976 Phase: 4 alt: 3151.375000

RSSI: -96

Got: Time: 14214144 Phase: 4 alt: 3137.875000

RSSI: -89

Got: Time: 14214313 Phase: 4 alt: 3131.437500

RSSI: -88

Got: Time: 14214482 Phase: 4 alt: 3130.312500

RSSI: -95

Got: Time: 14214651 Phase: 4 alt: 3126.312500

RSSI: -95

Got: Time: 14214821 Phase: 4 alt: 3128.562500

RSSI: -97

Got: Time: 14214990 Phase: 4 alt: 3125.875000

RSSI: -95

Got: Time: 14215332 Phase: 4 alt: 3118.750000

RSSI: -100

Got: Time: 14215500 Phase: 4 alt: 3117.437500

RSSI: -104

Got: Time: 14215671 Phase: 4 alt: 3110.750000

RSSI: -98

Got: Time: 14215840 Phase: 4 alt: 3097.375000

RSSI: -97

Got: Time: 14216010 Phase: 4 alt: 3089.437500

RSSI: -102

Got: Time: 14216181 Phase: 4 alt: 3092.875000

RSSI: -97

Got: Time: 14216350 Phase: 4 alt: 3092.437500

RSSI: -99

Got: Time: 14216520 Phase: 4 alt: 3088.250000

RSSI: -99

Got: Time: 14216689 Phase: 4 alt: 3085.562500

RSSI: -99

Got: Time: 14216857 Phase: 4 alt: 3077.562500

RSSI: -101

Got: Time: 14217026 Phase: 4 alt: 3064.625000

RSSI: -91

Got: Time: 14217195 Phase: 4 alt: 3058.812500

RSSI: -93

Got: Time: 14217365 Phase: 4 alt: 3065.750000

RSSI: -95

Got: Time: 14217536 Phase: 4 alt: 3064.500000

RSSI: -95

Got: Time: 14217705 Phase: 4 alt: 3055.250000

RSSI: -96

Got: Time: 14217876 Phase: 4 alt: 3057.750000

RSSI: -100

Got: Time: 14218045 Phase: 4 alt: 3050.500000

RSSI: -95

Got: Time: 14218386 Phase: 4 alt: 3027.562500

RSSI: -111

Got: Time: 14218555 Phase: 4 alt: 3031.125000

RSSI: -101

Got: Time: 14218726 Phase: 4 alt: 3031.875000

RSSI: -97

Got: Time: 14218894 Phase: 4 alt: 3031.250000

RSSI: -101

Got: Time: 14219064 Phase: 4 alt: 3031.437500

RSSI: -98

Got: Time: 14219234 Phase: 4 alt: 3032.187500

RSSI: -102

Got: Time: 14219741 Phase: 4 alt: 3007.875000

RSSI: -100

Got: Time: 14219910 Phase: 4 alt: 3003.875000

RSSI: -91

Got: Time: 14220080 Phase: 4 alt: 2989.687500

RSSI: -101

Got: Time: 14220249 Phase: 4 alt: 2981.125000

RSSI: -103

Got: Time: 14220420 Phase: 4 alt: 2984.437500

RSSI: -109

Got: Time: 14220591 Phase: 4 alt: 2979.437500

RSSI: -113

Got: Time: 14220760 Phase: 4 alt: 2979.500000

RSSI: -113

Got: Time: 14220930 Phase: 4 alt: 2975.000000

RSSI: -102

Got: Time: 14221099 Phase: 4 alt: 2977.187500

RSSI: -96

Got: Time: 14221270 Phase: 4 alt: 2958.812500

RSSI: -107

Got: Time: 14221441 Phase: 4 alt: 2961.562500

RSSI: -107

Got: Time: 14221609 Phase: 4 alt: 2959.625000

RSSI: -106

Got: Time: 14221779 Phase: 4 alt: 2947.562500

RSSI: -102

Got: Time: 14221948 Phase: 4 alt: 2947.687500

RSSI: -106

Got: Time: 14222286 Phase: 4 alt: 2935.625000

RSSI: -105

Got: Time: 14222454 Phase: 4 alt: 2926.375000

RSSI: -104

Got: Time: 14222625 Phase: 4 alt: 2921.312500

RSSI: -116

Got: Time: 14222796 Phase: 4 alt: 2921.875000

RSSI: -102

Got: Time: 14222964 Phase: 4 alt: 2927.312500

RSSI: -105

Got: Time: 14223474 Phase: 4 alt: 2899.500000

RSSI: -109

Got: Time: 14223645 Phase: 4 alt: 2903.062500

RSSI: -106

Got: Time: 14223814 Phase: 4 alt: 2897.000000

RSSI: -98

Got: Time: 14223984 Phase: 4 alt: 2894.625000

RSSI: -111

Got: Time: 14224322 Phase: 4 alt: 2883.000000

RSSI: -95

Got: Time: 14224490 Phase: 4 alt: 2883.812500

RSSI: -96

Got: Time: 14224659 Phase: 4 alt: 2882.437500

RSSI: -106

Got: Time: 14224829 Phase: 4 alt: 2878.125000

RSSI: -104

Got: Time: 14225000 Phase: 4 alt: 2873.875000

RSSI: -97

Got: Time: 14225168 Phase: 4 alt: 2866.812500

RSSI: -96

Got: Time: 14225339 Phase: 4 alt: 2867.687500

RSSI: -111

Got: Time: 14225508 Phase: 4 alt: 2853.875000

RSSI: -103

Got: Time: 14225679 Phase: 4 alt: 2850.187500

RSSI: -106

Got: Time: 14225849 Phase: 4 alt: 2853.250000

RSSI: -101

Got: Time: 14226018 Phase: 4 alt: 2845.500000

RSSI: -105

Got: Time: 14226189 Phase: 4 alt: 2840.187500

RSSI: -98

Got: Time: 14226357 Phase: 4 alt: 2829.937500

RSSI: -90

Got: Time: 14226527 Phase: 4 alt: 2823.687500

RSSI: -97

Got: Time: 14226696 Phase: 4 alt: 2828.437500

RSSI: -99

Got: Time: 14226864 Phase: 4 alt: 2825.000000

RSSI: -98

Got: Time: 14227034 Phase: 4 alt: 2825.875000

RSSI: -110

Got: Time: 14227372 Phase: 4 alt: 2813.625000

RSSI: -96

Got: Time: 14227543 Phase: 4 alt: 2806.875000

RSSI: -100

Got: Time: 14227712 Phase: 4 alt: 2804.625000

RSSI: -104

Got: Time: 14227883 Phase: 4 alt: 2804.000000

RSSI: -105

Got: Time: 14228053 Phase: 4 alt: 2802.625000

RSSI: -97

Got: Time: 14228222 Phase: 4 alt: 2794.125000

RSSI: -95

Got: Time: 14228393 Phase: 4 alt: 2783.500000

RSSI: -100

Got: Time: 14228562 Phase: 4 alt: 2787.375000

RSSI: -98

Got: Time: 14228731 Phase: 4 alt: 2782.062500

RSSI: -95

Got: Time: 14228900 Phase: 4 alt: 2774.750000

RSSI: -102

Got: Time: 14229068 Phase: 4 alt: 2765.625000

RSSI: -98

Got: Time: 14229577 Phase: 4 alt: 2757.437500

RSSI: -102

Got: Time: 14229747 Phase: 4 alt: 2750.625000

RSSI: -105

Got: Time: 14229916 Phase: 4 alt: 2744.187500

RSSI: -102

Got: Time: 14230087 Phase: 4 alt: 2734.625000

RSSI: -105

Got: Time: 14230258 Phase: 4 alt: 2735.750000

RSSI: -97

Got: Time: 14230426 Phase: 4 alt: 2733.937500

RSSI: -97

Got: Time: 14230597 Phase: 4 alt: 2733.062500

RSSI: -106

Got: Time: 14230766 Phase: 4 alt: 2727.562500

RSSI: -100

Got: Time: 14230936 Phase: 4 alt: 2716.750000

RSSI: -97

Got: Time: 14231105 Phase: 4 alt: 2710.062500

RSSI: -97

Got: Time: 14231273 Phase: 4 alt: 2701.312500

RSSI: -106

Got: Time: 14231442 Phase: 4 alt: 2701.375000

RSSI: -108

Got: Time: 14231612 Phase: 4 alt: 2704.312500

RSSI: -104

Got: Time: 14231781 Phase: 4 alt: 2705.312500

RSSI: -100

Got: Time: 14231951 Phase: 4 alt: 2699.812500

RSSI: -97

Got: Time: 14232120 Phase: 4 alt: 2689.062500

RSSI: -93

Got: Time: 14232291 Phase: 4 alt: 2685.062500

RSSI: -91

Got: Time: 14232462 Phase: 4 alt: 2675.500000

RSSI: -88

Got: Time: 14232630 Phase: 4 alt: 2667.437500

RSSI: -90

Got: Time: 14232801 Phase: 4 alt: 2669.687500

RSSI: -96

Got: Time: 14232970 Phase: 4 alt: 2673.250000

RSSI: -97

Got: Time: 14233140 Phase: 4 alt: 2668.750000

RSSI: -88

Got: Time: 14233310 Phase: 4 alt: 2655.875000

RSSI: -90

Got: Time: 14233478 Phase: 4 alt: 2654.062500

RSSI: -97

Got: Time: 14233647 Phase: 4 alt: 2645.375000

RSSI: -101

Got: Time: 14233816 Phase: 4 alt: 2649.250000

RSSI: -92

Got: Time: 14233985 Phase: 4 alt: 2638.062500

RSSI: -91

Got: Time: 14234156 Phase: 4 alt: 2628.062500

RSSI: -102

Got: Time: 14234324 Phase: 4 alt: 2620.250000

RSSI: -101

Got: Time: 14234495 Phase: 4 alt: 2624.312500

RSSI: -108

Got: Time: 14234666 Phase: 4 alt: 2624.937500

RSSI: -108

Got: Time: 14234835 Phase: 4 alt: 2622.750000

RSSI: -101

Got: Time: 14235005 Phase: 4 alt: 2610.437500

RSSI: -102

Got: Time: 14235174 Phase: 4 alt: 2602.312500

RSSI: -96

Got: Time: 14235345 Phase: 4 alt: 2602.187500

RSSI: -105

Got: Time: 14235515 Phase: 4 alt: 2606.687500

RSSI: -113

Got: Time: 14235684 Phase: 4 alt: 2597.875000

RSSI: -96

Got: Time: 14235853 Phase: 4 alt: 2589.312500

RSSI: -99

Got: Time: 14236022 Phase: 4 alt: 2579.250000

RSSI: -95

Got: Time: 14236191 Phase: 4 alt: 2581.875000

RSSI: -91

Got: Time: 14236360 Phase: 4 alt: 2584.000000

RSSI: -106

Got: Time: 14236529 Phase: 4 alt: 2573.187500

RSSI: -105

Got: Time: 14236700 Phase: 4 alt: 2566.875000

RSSI: -101

Got: Time: 14236871 Phase: 4 alt: 2562.375000

RSSI: -105

Got: Time: 14237039 Phase: 4 alt: 2555.875000

RSSI: -98

Got: Time: 14237210 Phase: 4 alt: 2554.625000

RSSI: -93

Got: Time: 14237379 Phase: 4 alt: 2542.812500

RSSI: -93

Got: Time: 14237549 Phase: 4 alt: 2541.500000

RSSI: -104

Got: Time: 14237720 Phase: 4 alt: 2548.187500

RSSI: -100

Got: Time: 14237889 Phase: 4 alt: 2540.500000

RSSI: -89

Got: Time: 14238059 Phase: 4 alt: 2533.562500

RSSI: -90

Got: Time: 14238228 Phase: 4 alt: 2526.187500

RSSI: -88

Got: Time: 14238397 Phase: 4 alt: 2529.125000

RSSI: -89

Got: Time: 14238566 Phase: 4 alt: 2524.625000

RSSI: -102

Got: Time: 14238734 Phase: 4 alt: 2518.375000

RSSI: -103

Got: Time: 14238904 Phase: 4 alt: 2515.062500

RSSI: -99

Got: Time: 14239075 Phase: 4 alt: 2510.625000

RSSI: -95

Got: Time: 14239244 Phase: 4 alt: 2496.937500

RSSI: -93

Got: Time: 14239415 Phase: 4 alt: 2495.187500

RSSI: -93

Got: Time: 14239583 Phase: 4 alt: 2489.437500

RSSI: -100

Got: Time: 14239754 Phase: 4 alt: 2488.125000

RSSI: -109

Got: Time: 14239925 Phase: 4 alt: 2486.312500

RSSI: -89

Got: Time: 14240264 Phase: 4 alt: 2477.250000

RSSI: -96

Got: Time: 14240433 Phase: 4 alt: 2478.437500

RSSI: -100

Got: Time: 14240602 Phase: 4 alt: 2472.500000

RSSI: -103

Got: Time: 14240771 Phase: 4 alt: 2471.937500

RSSI: -101

Got: Time: 14240940 Phase: 4 alt: 2462.125000

RSSI: -102

Got: Time: 14241109 Phase: 4 alt: 2454.187500

RSSI: -93

Got: Time: 14241279 Phase: 4 alt: 2450.187500

RSSI: -102

Got: Time: 14241449 Phase: 4 alt: 2443.562500

RSSI: -106

Got: Time: 14241619 Phase: 4 alt: 2445.437500

RSSI: -104

Got: Time: 14241788 Phase: 4 alt: 2446.250000

RSSI: -101

Got: Time: 14242129 Phase: 4 alt: 2431.750000

RSSI: -103

Got: Time: 14242298 Phase: 4 alt: 2425.625000

RSSI: -89

Got: Time: 14242469 Phase: 4 alt: 2416.812500

RSSI: -97

Got: Time: 14242637 Phase: 4 alt: 2426.187500

RSSI: -100

Got: Time: 14242808 Phase: 4 alt: 2427.250000

RSSI: -99

Got: Time: 14242978 Phase: 4 alt: 2420.312500

RSSI: -102

Got: Time: 14243315 Phase: 4 alt: 2403.312500

RSSI: -100

Got: Time: 14243484 Phase: 4 alt: 2397.000000

RSSI: -104

Got: Time: 14243653 Phase: 4 alt: 2396.375000

RSSI: -103

Got: Time: 14243823 Phase: 4 alt: 2395.500000

RSSI: -103

Got: Time: 14243992 Phase: 4 alt: 2391.937500

RSSI: -102

Got: Time: 14244163 Phase: 4 alt: 2382.625000

RSSI: -97

Got: Time: 14244334 Phase: 4 alt: 2381.250000

RSSI: -92

Got: Time: 14244502 Phase: 4 alt: 2371.125000

RSSI: -102

Got: Time: 14244673 Phase: 4 alt: 2370.375000

RSSI: -109

Got: Time: 14244842 Phase: 4 alt: 2379.500000

RSSI: -90

Got: Time: 14245013 Phase: 4 alt: 2369.187500

RSSI: -87

Got: Time: 14245352 Phase: 4 alt: 2357.375000

RSSI: -89

Got: Time: 14245522 Phase: 4 alt: 2348.437500

RSSI: -112

Got: Time: 14245691 Phase: 4 alt: 2350.312500

RSSI: -102

Got: Time: 14245860 Phase: 4 alt: 2349.062500

RSSI: -92

Got: Time: 14246028 Phase: 4 alt: 2338.937500

RSSI: -91

Got: Time: 14246197 Phase: 4 alt: 2344.750000

RSSI: -95

Got: Time: 14246368 Phase: 4 alt: 2344.187500

RSSI: -97

Got: Time: 14246538 Phase: 4 alt: 2339.812500

RSSI: -102

Got: Time: 14246707 Phase: 4 alt: 2318.125000

RSSI: -98

Got: Time: 14246878 Phase: 4 alt: 2321.750000

RSSI: -99

Got: Time: 14247046 Phase: 4 alt: 2324.437500

RSSI: -91

Got: Time: 14247217 Phase: 4 alt: 2319.687500

RSSI: -90

Got: Time: 14247557 Phase: 4 alt: 2303.750000

RSSI: -87

Got: Time: 14247727 Phase: 4 alt: 2301.312500

RSSI: -92

Got: Time: 14247896 Phase: 4 alt: 2302.812500

RSSI: -102

Got: Time: 14248065 Phase: 4 alt: 2297.250000

RSSI: -91

Got: Time: 14248234 Phase: 4 alt: 2302.812500

RSSI: -91

Got: Time: 14248403 Phase: 4 alt: 2297.937500

RSSI: -89

Got: Time: 14248572 Phase: 4 alt: 2285.312500

RSSI: -99

Got: Time: 14248742 Phase: 4 alt: 2276.500000

RSSI: -106

Got: Time: 14248911 Phase: 4 alt: 2276.625000

RSSI: -101

Got: Time: 14249082 Phase: 4 alt: 2279.500000

RSSI: -106

Got: Time: 14249421 Phase: 4 alt: 2269.812500

RSSI: -88

Got: Time: 14249592 Phase: 4 alt: 2273.125000

RSSI: -93

Got: Time: 14249761 Phase: 4 alt: 2265.375000

RSSI: -95

Got: Time: 14249932 Phase: 4 alt: 2259.437500

RSSI: -93

Got: Time: 14250100 Phase: 4 alt: 2261.437500

RSSI: -102

Got: Time: 14250270 Phase: 4 alt: 2253.312500

RSSI: -92

Got: Time: 14250438 Phase: 4 alt: 2253.562500

RSSI: -98

Got: Time: 14250607 Phase: 4 alt: 2248.875000

RSSI: -90

Got: Time: 14250776 Phase: 4 alt: 2237.062500

RSSI: -103

Got: Time: 14250947 Phase: 4 alt: 2231.312500

RSSI: -98

Got: Time: 14251116 Phase: 4 alt: 2224.562500

RSSI: -87

Got: Time: 14251286 Phase: 4 alt: 2229.312500

RSSI: -86

Got: Time: 14251455 Phase: 4 alt: 2229.062500

RSSI: -93

Got: Time: 14251626 Phase: 4 alt: 2219.062500

RSSI: -89

Got: Time: 14251796 Phase: 4 alt: 2215.812500

RSSI: -87

Got: Time: 14251965 Phase: 4 alt: 2205.437500

RSSI: -87

Got: Time: 14252136 Phase: 4 alt: 2201.062500

RSSI: -97

Got: Time: 14252305 Phase: 4 alt: 2197.500000

RSSI: -102

Got: Time: 14252475 Phase: 4 alt: 2191.562500

RSSI: -103

Got: Time: 14252644 Phase: 4 alt: 2196.375000

RSSI: -96

Got: Time: 14252813 Phase: 4 alt: 2192.937500

RSSI: -91

Got: Time: 14252981 Phase: 4 alt: 2187.062500

RSSI: -89

Got: Time: 14253151 Phase: 4 alt: 2186.687500

RSSI: -93

Got: Time: 14253320 Phase: 4 alt: 2175.000000

RSSI: -96

Got: Time: 14253491 Phase: 4 alt: 2180.750000

RSSI: -97

Got: Time: 14253659 Phase: 4 alt: 2170.250000

RSSI: -86

Got: Time: 14253830 Phase: 4 alt: 2169.562500

RSSI: -88

Got: Time: 14254001 Phase: 4 alt: 2164.500000

RSSI: -88

Got: Time: 14254170 Phase: 4 alt: 2160.437500

RSSI: -87

Got: Time: 14254340 Phase: 4 alt: 2152.812500

RSSI: -88

Got: Time: 14254509 Phase: 4 alt: 2158.750000

RSSI: -90

Got: Time: 14254680 Phase: 4 alt: 2155.312500

RSSI: -89

Got: Time: 14254851 Phase: 4 alt: 2145.187500

RSSI: -90

Got: Time: 14255019 Phase: 4 alt: 2139.625000

RSSI: -90

Got: Time: 14255189 Phase: 4 alt: 2132.875000

RSSI: -89

Got: Time: 14255358 Phase: 4 alt: 2129.750000

RSSI: -90

Got: Time: 14255527 Phase: 4 alt: 2134.000000

RSSI: -90

Got: Time: 14255696 Phase: 4 alt: 2136.062500

RSSI: -89

Got: Time: 14255864 Phase: 4 alt: 2132.312500

RSSI: -101

Got: Time: 14256035 Phase: 4 alt: 2122.437500

RSSI: -91

Got: Time: 14256205 Phase: 4 alt: 2120.937500

RSSI: -82

Got: Time: 14256375 Phase: 4 alt: 2102.687500

RSSI: -88

Got: Time: 14256545 Phase: 4 alt: 2110.875000

RSSI: -91

Got: Time: 14256714 Phase: 4 alt: 2110.312500

RSSI: -92

Got: Time: 14256885 Phase: 4 alt: 2095.187500

RSSI: -104

Got: Time: 14257056 Phase: 4 alt: 2090.312500

RSSI: -86

Got: Time: 14257224 Phase: 4 alt: 2084.500000

RSSI: -83

Got: Time: 14257395 Phase: 4 alt: 2084.312500

RSSI: -90

Got: Time: 14257564 Phase: 4 alt: 2085.437500

RSSI: -95

Got: Time: 14257734 Phase: 4 alt: 2086.500000

RSSI: -98

Got: Time: 14257903 Phase: 4 alt: 2082.937500

RSSI: -103

Got: Time: 14258072 Phase: 4 alt: 2068.875000

RSSI: -99

Got: Time: 14258240 Phase: 4 alt: 2062.062500

RSSI: -91

Got: Time: 14258410 Phase: 4 alt: 2064.687500

RSSI: -98

Got: Time: 14258580 Phase: 4 alt: 2062.187500

RSSI: -90

Got: Time: 14258750 Phase: 4 alt: 2056.562500

RSSI: -89

Got: Time: 14258919 Phase: 4 alt: 2052.687500

RSSI: -96

Got: Time: 14259089 Phase: 4 alt: 2044.687500

RSSI: -103

Got: Time: 14259260 Phase: 4 alt: 2047.875000

RSSI: -88

Got: Time: 14259429 Phase: 4 alt: 2044.750000

RSSI: -96

Got: Time: 14259600 Phase: 4 alt: 2033.125000

RSSI: -91

Got: Time: 14259768 Phase: 4 alt: 2028.000000

RSSI: -101

Got: Time: 14259939 Phase: 4 alt: 2027.375000

RSSI: -92

Got: Time: 14260110 Phase: 4 alt: 2037.437500

RSSI: -96

Got: Time: 14260279 Phase: 4 alt: 2029.750000

RSSI: -113

Got: Time: 14260449 Phase: 4 alt: 2020.500000

RSSI: -102

Got: Time: 14260617 Phase: 4 alt: 2015.812500

RSSI: -100

Got: Time: 14260786 Phase: 4 alt: 2012.125000

RSSI: -92

Got: Time: 14260955 Phase: 4 alt: 2011.687500

RSSI: -92

Got: Time: 14261124 Phase: 4 alt: 2001.812500

RSSI: -92

Got: Time: 14261294 Phase: 4 alt: 1990.750000

RSSI: -100

Got: Time: 14261465 Phase: 4 alt: 2005.625000

RSSI: -101

Got: Time: 14261633 Phase: 4 alt: 2000.125000

RSSI: -98

Got: Time: 14261804 Phase: 4 alt: 1995.750000

RSSI: -95

Got: Time: 14261973 Phase: 4 alt: 1993.375000

RSSI: -95

Got: Time: 14262144 Phase: 4 alt: 1987.937500

RSSI: -92

Got: Time: 14262314 Phase: 4 alt: 1985.812500

RSSI: -99

Got: Time: 14262483 Phase: 4 alt: 1980.062500

RSSI: -96

Got: Time: 14262654 Phase: 4 alt: 1973.250000

RSSI: -89

Got: Time: 14262822 Phase: 4 alt: 1968.750000

RSSI: -88

Got: Time: 14262992 Phase: 4 alt: 1965.187500

RSSI: -87

Got: Time: 14263160 Phase: 4 alt: 1963.750000

RSSI: -91

Got: Time: 14263329 Phase: 4 alt: 1958.125000

RSSI: -83

Got: Time: 14263499 Phase: 4 alt: 1946.125000

RSSI: -84

Got: Time: 14263669 Phase: 4 alt: 1951.187500

RSSI: -84

Got: Time: 14263838 Phase: 4 alt: 1948.500000

RSSI: -95

Got: Time: 14264009 Phase: 4 alt: 1936.937500

RSSI: -88

Got: Time: 14264177 Phase: 4 alt: 1928.375000

RSSI: -81

Got: Time: 14264348 Phase: 4 alt: 1921.625000

RSSI: -84

Got: Time: 14264519 Phase: 4 alt: 1925.000000

RSSI: -89

Got: Time: 14264688 Phase: 4 alt: 1927.437500

RSSI: -91

Got: Time: 14264858 Phase: 4 alt: 1921.687500

RSSI: -89

Got: Time: 14265027 Phase: 4 alt: 1914.812500

RSSI: -84

Got: Time: 14265197 Phase: 4 alt: 1905.500000

RSSI: -88

Got: Time: 14265366 Phase: 4 alt: 1904.187500

RSSI: -88

Got: Time: 14265535 Phase: 4 alt: 1902.625000

RSSI: -100

Got: Time: 14265704 Phase: 4 alt: 1897.875000

RSSI: -89

Got: Time: 14265873 Phase: 4 alt: 1893.500000

RSSI: -98

Got: Time: 14266042 Phase: 4 alt: 1890.437500

RSSI: -104

Got: Time: 14266213 Phase: 4 alt: 1886.375000

RSSI: -99

Got: Time: 14266381 Phase: 4 alt: 1884.062500

RSSI: -88

Got: Time: 14266552 Phase: 4 alt: 1878.562500

RSSI: -92

Got: Time: 14266723 Phase: 4 alt: 1870.187500

RSSI: -84

Got: Time: 14266892 Phase: 4 alt: 1870.687500

RSSI: -86

Got: Time: 14267062 Phase: 4 alt: 1873.937500

RSSI: -96

Got: Time: 14267231 Phase: 4 alt: 1871.125000

RSSI: -91

Got: Time: 14267401 Phase: 4 alt: 1862.937500

RSSI: -96

Got: Time: 14267572 Phase: 4 alt: 1863.562500

RSSI: -89

Got: Time: 14267741 Phase: 4 alt: 1865.687500

RSSI: -87

Got: Time: 14267909 Phase: 4 alt: 1848.000000

RSSI: -96

Got: Time: 14268078 Phase: 4 alt: 1842.125000

RSSI: -90

Got: Time: 14268247 Phase: 4 alt: 1848.437500

RSSI: -103

Got: Time: 14268417 Phase: 4 alt: 1842.875000

RSSI: -92

Got: Time: 14268586 Phase: 4 alt: 1829.312500

RSSI: -91

Got: Time: 14268756 Phase: 4 alt: 1837.812500

RSSI: -103

Got: Time: 14268927 Phase: 4 alt: 1824.312500

RSSI: -101

Got: Time: 14269096 Phase: 4 alt: 1821.250000

RSSI: -81

Got: Time: 14269267 Phase: 4 alt: 1810.562500

RSSI: -93

Got: Time: 14269436 Phase: 4 alt: 1812.562500

RSSI: -85

Got: Time: 14269606 Phase: 4 alt: 1812.312500

RSSI: -83

Got: Time: 14269777 Phase: 4 alt: 1801.250000

RSSI: -96

Got: Time: 14269946 Phase: 4 alt: 1799.437500

RSSI: -95

Got: Time: 14270116 Phase: 4 alt: 1796.750000

RSSI: -97

Got: Time: 14270284 Phase: 4 alt: 1790.625000

RSSI: -103

Got: Time: 14270453 Phase: 4 alt: 1786.250000

RSSI: -95

Got: Time: 14270622 Phase: 4 alt: 1789.062500

RSSI: -100

Got: Time: 14270791 Phase: 4 alt: 1784.500000

RSSI: -98

Got: Time: 14270961 Phase: 4 alt: 1778.375000

RSSI: -97

Got: Time: 14271132 Phase: 4 alt: 1773.125000

RSSI: -97

Got: Time: 14271300 Phase: 4 alt: 1766.937500

RSSI: -101

Got: Time: 14271471 Phase: 4 alt: 1764.562500

RSSI: -91

Got: Time: 14271640 Phase: 4 alt: 1760.750000

RSSI: -97

Got: Time: 14271811 Phase: 4 alt: 1764.437500

RSSI: -98

Got: Time: 14271981 Phase: 4 alt: 1763.687500

RSSI: -102

Got: Time: 14272150 Phase: 4 alt: 1757.875000

RSSI: -95

Got: Time: 14272321 Phase: 4 alt: 1755.500000

RSSI: -101

Got: Time: 14272489 Phase: 4 alt: 1749.750000

RSSI: -97

Got: Time: 14272658 Phase: 4 alt: 1744.937500

RSSI: -88

Got: Time: 14272827 Phase: 4 alt: 1739.375000

RSSI: -88

Got: Time: 14272827 Phase: 5 alt: 1712.500000

RSSI: -87

Got: Time: 14274208 Phase: 5 alt: 1702.687500

RSSI: -85

Got: Time: 14274377 Phase: 5 alt: 1697.437500

RSSI: -83

Got: Time: 14274545 Phase: 5 alt: 1695.437500

RSSI: -85

Got: Time: 14274714 Phase: 5 alt: 1692.562500

RSSI: -87

Got: Time: 14274884 Phase: 5 alt: 1690.687500

RSSI: -88

Got: Time: 14275054 Phase: 5 alt: 1681.000000

RSSI: -89

Got: Time: 14275223 Phase: 5 alt: 1684.000000

RSSI: -86

Got: Time: 14275394 Phase: 5 alt: 1685.750000

RSSI: -85

Got: Time: 14275563 Phase: 5 alt: 1680.062500

RSSI: -83

Got: Time: 14275733 Phase: 5 alt: 1674.625000

RSSI: -91

Got: Time: 14275904 Phase: 5 alt: 1667.437500

RSSI: -100

Got: Time: 14276073 Phase: 5 alt: 1662.875000

RSSI: -89

Got: Time: 14276243 Phase: 5 alt: 1658.000000

RSSI: -87

Got: Time: 14276412 Phase: 5 alt: 1651.125000

RSSI: -96

Got: Time: 14276582 Phase: 5 alt: 1651.000000

RSSI: -93

Got: Time: 14276750 Phase: 5 alt: 1648.875000

RSSI: -87

Got: Time: 14276919 Phase: 5 alt: 1643.250000

RSSI: -86

Got: Time: 14277088 Phase: 5 alt: 1641.125000

RSSI: -87

Got: Time: 14277259 Phase: 5 alt: 1639.812500

RSSI: -82

Got: Time: 14277427 Phase: 5 alt: 1626.125000

RSSI: -84

Got: Time: 14277598 Phase: 5 alt: 1625.250000

RSSI: -87

Got: Time: 14277767 Phase: 5 alt: 1625.562500

RSSI: -81

Got: Time: 14277938 Phase: 5 alt: 1620.625000

RSSI: -89

Got: Time: 14278108 Phase: 5 alt: 1619.000000

RSSI: -85

Got: Time: 14278277 Phase: 5 alt: 1615.312500

RSSI: -95

Got: Time: 14278448 Phase: 5 alt: 1607.000000

RSSI: -101

Got: Time: 14278616 Phase: 5 alt: 1601.812500

RSSI: -85

Got: Time: 14278786 Phase: 5 alt: 1602.750000

RSSI: -85

Got: Time: 14278955 Phase: 5 alt: 1603.687500

RSSI: -84

Got: Time: 14279124 Phase: 5 alt: 1603.750000

RSSI: -92

Got: Time: 14279293 Phase: 5 alt: 1591.500000

RSSI: -86

Got: Time: 14279463 Phase: 5 alt: 1452.812500

RSSI: -93

Got: Time: 14279632 Phase: 5 alt: 1567.812500

RSSI: -96

Got: Time: 14279803 Phase: 5 alt: 1590.750000

RSSI: -97

Got: Time: 14279971 Phase: 5 alt: 1584.562500

RSSI: -91

Got: Time: 14280142 Phase: 5 alt: 1582.187500

RSSI: -92

Got: Time: 14280313 Phase: 5 alt: 1567.937500

RSSI: -91

Got: Time: 14280481 Phase: 5 alt: 1567.312500

RSSI: -96

Got: Time: 14280652 Phase: 5 alt: 1562.875000

RSSI: -113

Got: Time: 14280821 Phase: 5 alt: 1559.187500

RSSI: -90

Got: Time: 14280991 Phase: 5 alt: 1564.375000

RSSI: -92

Got: Time: 14281161 Phase: 5 alt: 1552.062500

RSSI: -79

Got: Time: 14281330 Phase: 5 alt: 1542.937500

RSSI: -80

Got: Time: 14281498 Phase: 5 alt: 1543.000000

RSSI: -88

Got: Time: 14281667 Phase: 5 alt: 1545.000000

RSSI: -86

Got: Time: 14281837 Phase: 5 alt: 1543.500000

RSSI: -109

Got: Time: 14282007 Phase: 5 alt: 1544.062500

RSSI: -88

Got: Time: 14282176 Phase: 5 alt: 1525.687500

RSSI: -87

Got: Time: 14282346 Phase: 5 alt: 1521.250000

RSSI: -89

Got: Time: 14282517 Phase: 5 alt: 1522.750000

RSSI: -95

Got: Time: 14282686 Phase: 5 alt: 1519.000000

RSSI: -85

Got: Time: 14282857 Phase: 5 alt: 1510.812500

RSSI: -96

Got: Time: 14283025 Phase: 5 alt: 1508.875000

RSSI: -83

Got: Time: 14283196 Phase: 5 alt: 1501.625000

RSSI: -81

Got: Time: 14283367 Phase: 5 alt: 1496.687500

RSSI: -92

Got: Time: 14283536 Phase: 5 alt: 1493.812500

RSSI: -90

Got: Time: 14283706 Phase: 5 alt: 1488.000000

RSSI: -85

Got: Time: 14283874 Phase: 5 alt: 1492.687500

RSSI: -99

Got: Time: 14284043 Phase: 5 alt: 1489.625000

RSSI: -87

Got: Time: 14284212 Phase: 5 alt: 1482.000000

RSSI: -87

Got: Time: 14284381 Phase: 5 alt: 1477.750000

RSSI: -90

Got: Time: 14284551 Phase: 5 alt: 1470.687500

RSSI: -89

Got: Time: 14284722 Phase: 5 alt: 1463.750000

RSSI: -87

Got: Time: 14284891 Phase: 5 alt: 1463.625000

RSSI: -90

Got: Time: 14285062 Phase: 5 alt: 1463.875000

RSSI: -87

Got: Time: 14285230 Phase: 5 alt: 1458.250000

RSSI: -90

Got: Time: 14285401 Phase: 5 alt: 1457.250000

RSSI: -95

Got: Time: 14285572 Phase: 5 alt: 1454.437500

RSSI: -84

Got: Time: 14285741 Phase: 5 alt: 1449.687500

RSSI: -83

Got: Time: 14285911 Phase: 5 alt: 1449.312500

RSSI: -92

Got: Time: 14286080 Phase: 5 alt: 1447.375000

RSSI: -88

Got: Time: 14286250 Phase: 5 alt: 1435.312500

RSSI: -86

Got: Time: 14286419 Phase: 5 alt: 1439.125000

RSSI: -93

Got: Time: 14286588 Phase: 5 alt: 1432.687500

RSSI: -85

Got: Time: 14286757 Phase: 5 alt: 1420.812500

RSSI: -90

Got: Time: 14286926 Phase: 5 alt: 1419.437500

RSSI: -92

Got: Time: 14287096 Phase: 5 alt: 1417.875000

RSSI: -98

Got: Time: 14287435 Phase: 5 alt: 1411.937500

RSSI: -88

Got: Time: 14287606 Phase: 5 alt: 1406.125000

RSSI: -87

Got: Time: 14287777 Phase: 5 alt: 1405.437500

RSSI: -86

Got: Time: 14287946 Phase: 5 alt: 1395.562500

RSSI: -92

Got: Time: 14288116 Phase: 5 alt: 1389.000000

RSSI: -89

Got: Time: 14288285 Phase: 5 alt: 1388.250000

RSSI: -91

Got: Time: 14288456 Phase: 5 alt: 1388.187500

RSSI: -87

Got: Time: 14288627 Phase: 5 alt: 1387.875000

RSSI: -85

Got: Time: 14288795 Phase: 5 alt: 1381.187500

RSSI: -90

Got: Time: 14288965 Phase: 5 alt: 1374.687500

RSSI: -88

Got: Time: 14289134 Phase: 5 alt: 1366.500000

RSSI: -82

Got: Time: 14289303 Phase: 5 alt: 1366.875000

RSSI: -83

Got: Time: 14289472 Phase: 5 alt: 1363.312500

RSSI: -87

Got: Time: 14289640 Phase: 5 alt: 1362.125000

RSSI: -88

Got: Time: 14289811 Phase: 5 alt: 1356.562500

RSSI: -89

Got: Time: 14289981 Phase: 5 alt: 1352.187500

RSSI: -85

Got: Time: 14290150 Phase: 5 alt: 1350.375000

RSSI: -89

Got: Time: 14290321 Phase: 5 alt: 1347.437500

RSSI: -83

Got: Time: 14290490 Phase: 5 alt: 1342.312500

RSSI: -82

Got: Time: 14290660 Phase: 5 alt: 1339.812500

RSSI: -79

Got: Time: 14290831 Phase: 5 alt: 1332.125000

RSSI: -91

Got: Time: 14291000 Phase: 5 alt: 1327.125000

RSSI: -97

Got: Time: 14291170 Phase: 5 alt: 1320.250000

RSSI: -89

Got: Time: 14291339 Phase: 5 alt: 1315.437500

RSSI: -80

Got: Time: 14291508 Phase: 5 alt: 1315.000000

RSSI: -81

Got: Time: 14291677 Phase: 5 alt: 1308.125000

RSSI: -83

Got: Time: 14291846 Phase: 5 alt: 1304.875000

RSSI: -91

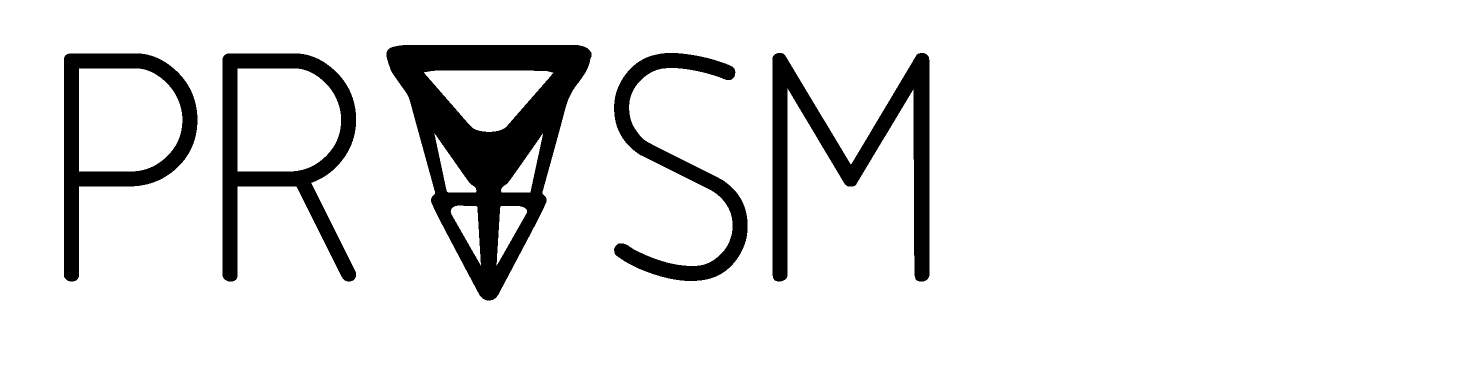
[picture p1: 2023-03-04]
hardware/Fall 2022/PRISM_IO/PRISM.bmp

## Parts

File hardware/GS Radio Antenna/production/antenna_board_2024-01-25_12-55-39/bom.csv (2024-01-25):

Designator | Footprint | Quantity | Value | LCSC Part #
C1 | 0603 | 1 | 0.47 uF
C2 | 0805 | 1 | 33 uF
C3 | 0603 | 1 | 10uF
H1, H2, H3, H4, H5 | MountingHole_3.2mm_M3_DIN965_Pad_TopBottom | 5 | MountingHole
J1 | PinSocket_1x02_P2.54mm_Vertical | 1 | Conn_01x02_Socket
R1, R2, R3 | 0603 | 3 | 1K
R4, R5, R6, R7 | 0603 | 4 | 20K
R8 | 0603 | 1 | 10k
R9 | 0603 | 1 | 33k
U1 | RFM69HCW_Breakout | 1 | ~
U10, U11, U12, U9 | PG-TO220-3_INF | 4 | IRF4905PBF
U2 | MODULE_ESP32-DEVKITC | 1 | ESP32-DEVKITC
U3 | LM3940IT | 1 | LM3940IT-3.3/NOPB
U4, U5, U6 | TLC5916IN | 3 | TLC5916IN
U7, U8 | Seven_Segment_Display | 2 | ~

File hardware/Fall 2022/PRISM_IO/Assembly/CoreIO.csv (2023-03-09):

Item | Quantity | Designator | Value | LibPart | Footprint | LCSC Part #
 |  | D1 | LED | Device:LED | LED_SMD:LED_0603_1608Metric | C2290
 |  | D2 | SS54 | SS54:SS54 | JLC_footprints:DO-214AC | C22452
 |  | D3 | SS54 | SS54:SS54 | JLC_footprints:DO-214AC | C22452
 |  | Q1 | AO3400A | AO3400A:AO3400A | AO3400A:SOT95P280X125-3N | C20917
 |  | Q2 | AO3400A | AO3400A:AO3400A | SOT95P280X125-3N | C20917
 |  | R1 | 150 | Device:R | Resistor_SMD:R_0603_1608Metric | C22808
 |  | R2 | 10k | Device:R | Resistor_SMD:R_0603_1608Metric | C25804
 |  | R5 | 10k | Device:R | Resistor_SMD:R_0603_1608Metric | C25804
 |  | R6 | 1M | Device:R | Resistor_SMD:R_0603_1608Metric | C22935
 |  | R7 | 10k | Device:R | Resistor_SMD:R_0603_1608Metric | C25804
 |  | R8 | 10k | Device:R | Resistor_SMD:R_0603_1608Metric | C25804
 |  | R9 | 1M | Device:R | Resistor_SMD:R_0603_1608Metric | C22935
 |  | R10 | 10k | Device:R | Resistor_SMD:R_0603_1608Metric | C25804
 |  | R11 | 10k | Device:R | Resistor_SMD:R_0603_1608Metric | C25804

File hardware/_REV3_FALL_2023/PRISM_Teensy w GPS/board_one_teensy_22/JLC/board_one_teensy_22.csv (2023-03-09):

Item | Qty | Designator | Value | LibPart | Footprint | LCSC Part #
 |  | C1 | 0.1uf | Device:C | Capacitor_SMD:C_0603_1608Metric | C14663
 |  | C2 | 0.1uf | Device:C | Capacitor_SMD:C_0603_1608Metric | C14663
 |  | D1 | SS54 | SS54:SS54 | JLC_footprints:DO-214AC | C22452
 |  | D2 | SS54 | SS54:SS54 | JLC_footprints:DO-214AC | C22452
 |  | R4 | 200K | Device:R | Resistor_SMD:R_0603_1608Metric | C25811
 |  | R5 | 300K | Device:R | Resistor_SMD:R_0603_1608Metric | C23024

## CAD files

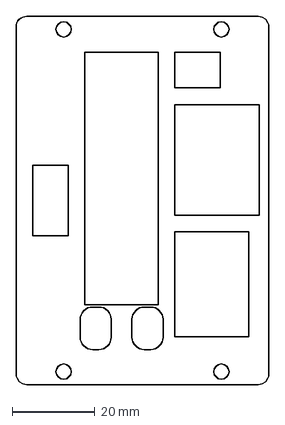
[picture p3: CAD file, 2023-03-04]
hardware/_REV3_FALL_2023/PRISM_Teensy w GPS/PRISM_MAIN_PCB_final.dxf
61.0 x 88.9 mm

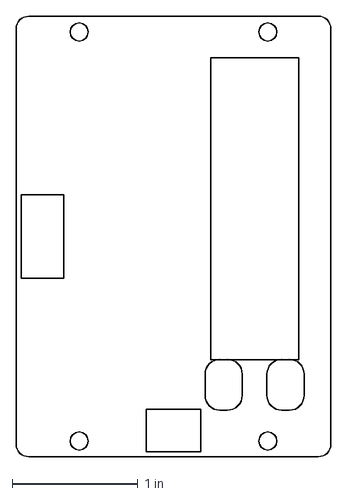
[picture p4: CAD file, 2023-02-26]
hardware/_REV3_FALL_2023/PRISM_Teensy w GPS/PRISM_MAIN_PCB_with_sd_clip_and_connectors.dxf
2.50 x 3.50 in

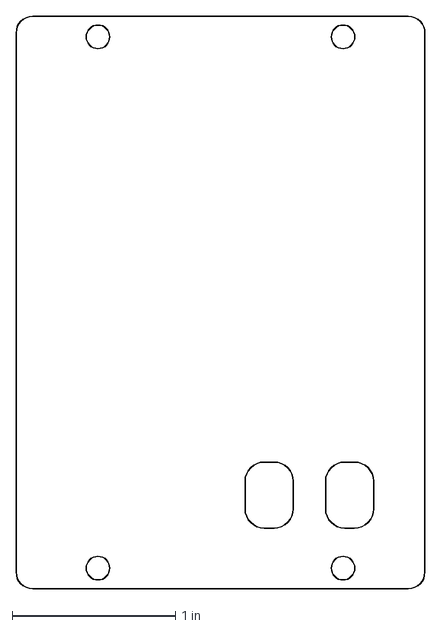
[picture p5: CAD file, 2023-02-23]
hardware/_REV3_FALL_2023/PRISM_Teensy w GPS/PRISM_MAIN_PCB_with_sd_clip.dxf
2.50 x 3.50 in

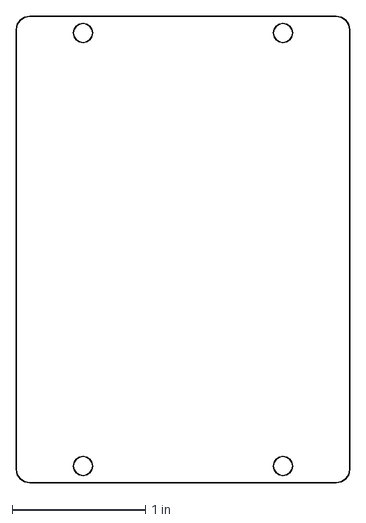
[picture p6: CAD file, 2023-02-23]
hardware/_REV3_FALL_2023/PRISM_Teensy w GPS/PRISM_MAIN_PCB.dxf
2.50 x 3.50 in

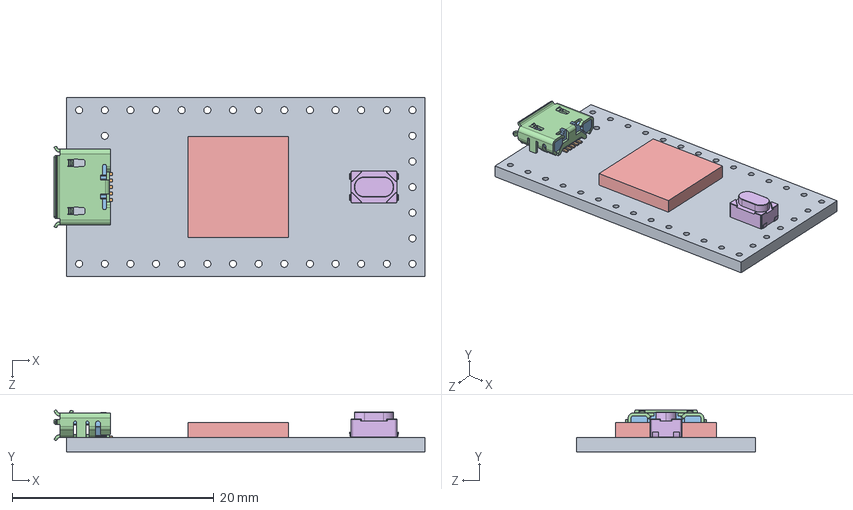
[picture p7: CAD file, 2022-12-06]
common_kicad_libraries/rocketry_footprints/Teensy_4.0_Assembly.STEP
36.8 x 4.12 x 17.7 mm
Teensy_4.0_PCB
Micro USB-B Female 5Pin SMD
NXP iMXRT1062
SKRPACE010 v4

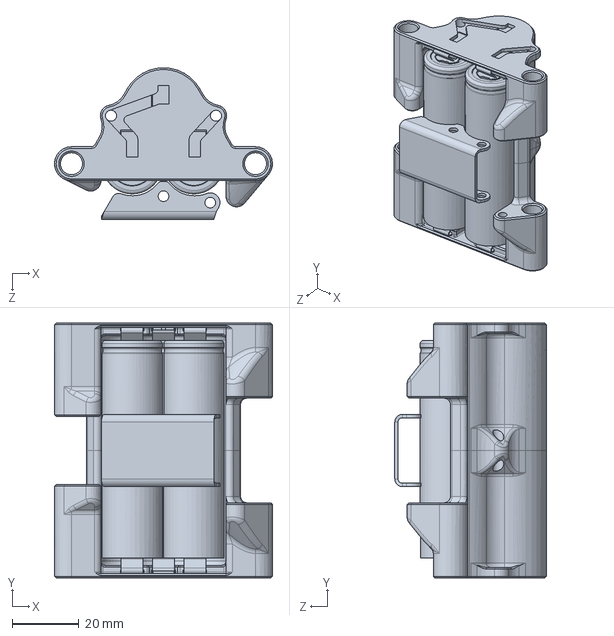
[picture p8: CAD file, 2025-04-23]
Avi Stucture/BT_01.SLDPRT
65.2 x 76.2 x 45.3 mm

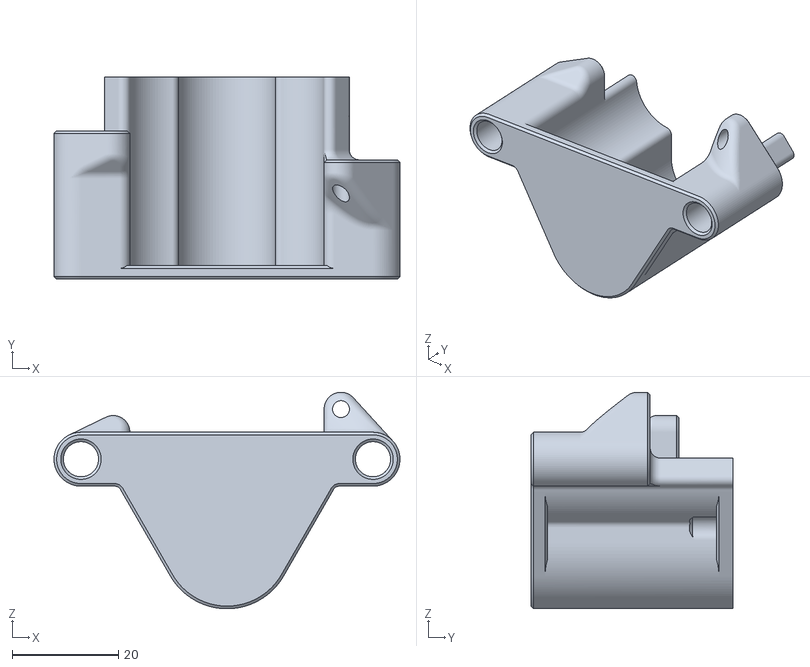
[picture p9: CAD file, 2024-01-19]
Avi Stucture/STLS/CASE.STL
65.2 x 38.1 x 40.8

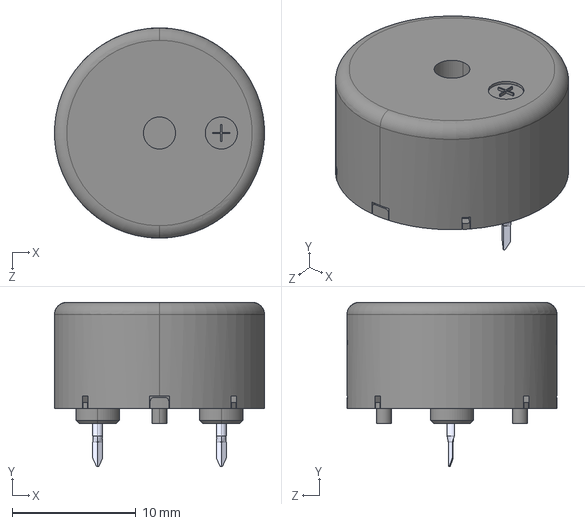
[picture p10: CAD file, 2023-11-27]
common_kicad_libraries/rocketry_footprints/PKM17EPP-2002-B0.step
17.0 x 13.3 x 17.0 mm

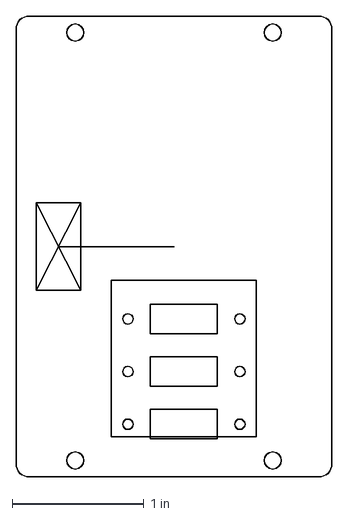
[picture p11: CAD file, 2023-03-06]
hardware/_REV3_FALL_2023/PRISM_IO/PRISM_IO_PCB_with_connectors.dxf
2.40 x 3.50 in

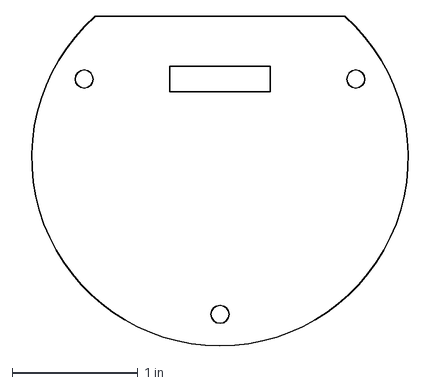
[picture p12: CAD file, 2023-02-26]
hardware/Fall 2022/EAST_GPS/EAST_PCB_no_sd_clip.dxf
3.25 x 2.62 in

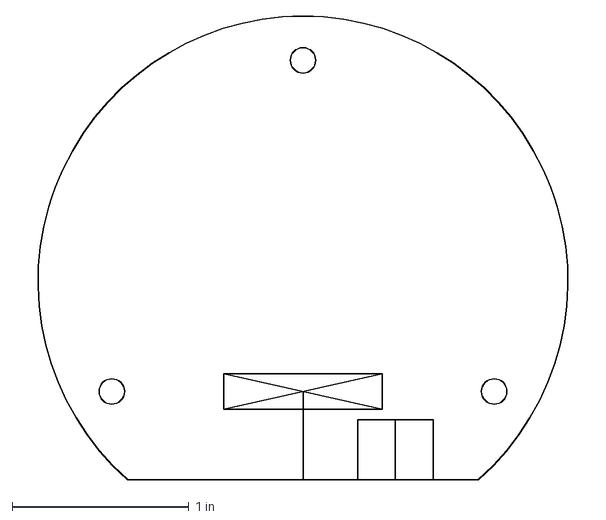
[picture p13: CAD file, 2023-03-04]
hardware/Fall 2022/EAST_Teensy/EAST_PCB_outline_final.dxf
3.25 x 2.63 in

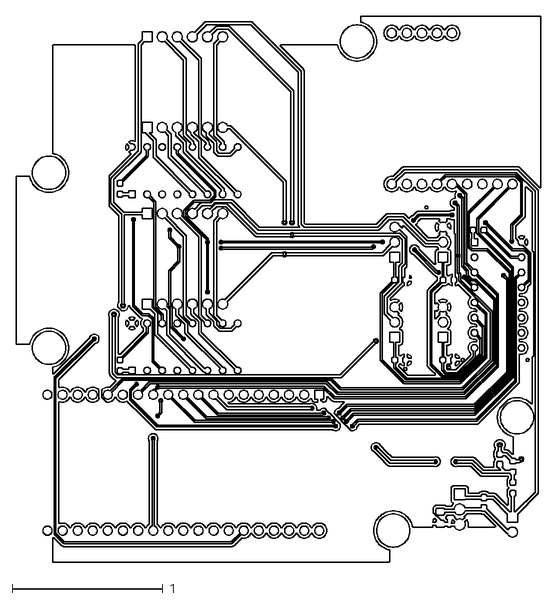
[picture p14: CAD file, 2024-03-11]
hardware/GS Radio Antenna/antenna_board-F_Cu.dxf
3.48 x 3.62

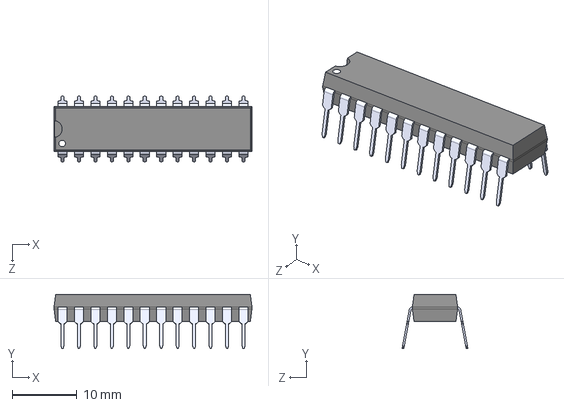
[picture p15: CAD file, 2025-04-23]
hardware/Radio_Board_Rev2/footprints/MAX7219CNG.step
30.5 x 8.38 x 10.2 mm

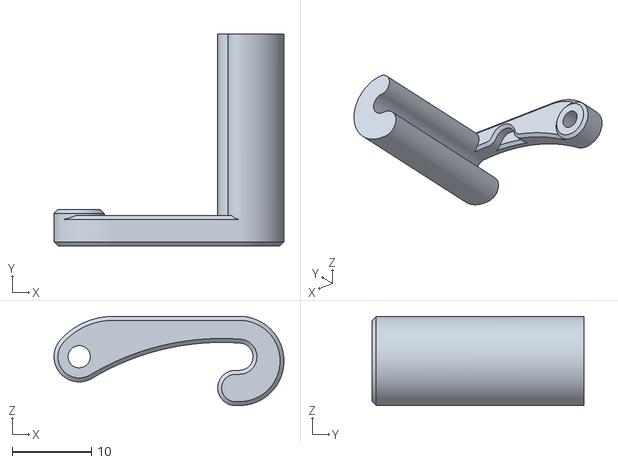
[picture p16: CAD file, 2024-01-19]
Avi Stucture/STLS/BUCKEL1.STL
29.0 x 26.7 x 11.2

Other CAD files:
Avi Stucture/MAIN.SLDASM
common_kicad_libraries/rocketry_footprints/WS2812B.step
hardware/_REV3_FALL_2023/PRISM_IO/CoreIO.step
Avi Stucture/18650 Li-Ion.SLDPRT
Avi Stucture/BHCS-4-40.SLDPRT
Avi Stucture/BT_01-Boss-Extrude9.SLDPRT
Avi Stucture/BT_01.SLDDRW
Avi Stucture/FR_01.SLDPRT
Avi Stucture/FR_02.SLDPRT
Avi Stucture/FR_03.SLDPRT
Avi Stucture/FR_04.SLDPRT
Avi Stucture/FR_05.SLDPRT
Avi Stucture/FR_06.SLDPRT
Avi Stucture/FR_07.SLDPRT
Avi Stucture/FR_08.SLDPRT
Avi Stucture/FR_09.SLDPRT
Avi Stucture/MASTER_SKETCH.SLDPRT
Avi Stucture/PRISM_FC.SLDPRT
Avi Stucture/PRISM_IO.SLDPRT
Avi Stucture/SHCS-6.SLDPRT
Avi Stucture/STLS/BUCKEL2.STL
Avi Stucture/STLS/FR_08.STL
Avi Stucture/STLS/LINK1.STL
Avi Stucture/legacy.SLDPRT
common_kicad_libraries/rocketry_footprints/1655.step
common_kicad_libraries/rocketry_footprints/D2F-01F.step
common_kicad_libraries/rocketry_footprints/DM3CS-SF.step
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

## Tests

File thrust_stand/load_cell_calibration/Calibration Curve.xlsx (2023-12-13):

Average Voltage 50x Scale (mV) | Average Voltage (mV) | Load (N)
-77.57959 | -1.5515918 | 0
-26.211183 | -0.52422366 | 118
1.096894 | 0.02193788 | 178
50.81235 | 1.016247 | 283
129.8654 | 2.597308 | 450
192.2635 | 3.84527 | 581
229.9685 | 4.59937 | 660
290.9231 | 5.818462 | 789
350.5512 | 7.011024 | 913
427.1896 | 8.543792 | 1075
494.1046 | 9.882092 | 1215
555.948 | 11.11896 | 1345
615.0533 | 12.301066 | 1460
680.5828 | 13.611656 | 1600
735.2319 | 14.704638 | 1715
798.6282 | 15.972564 | 1850
859.5644 | 17.191288 | 1975
920.1622 | 18.403244 | 2100
981.7477 | 19.634954 | 2230
1106.015 | 22.1203 | 2490

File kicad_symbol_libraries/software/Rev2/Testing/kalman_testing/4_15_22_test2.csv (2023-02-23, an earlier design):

Time since launch (ms) | X Acceleration (m/s) | Y Acceleration (m/s) | Z Acceleration (m/s) | X Orientation | Y Orientation | Z Orientation | Global Z Accel | Altitude (m) | Latitude | Longitude | Phase | Kalman Altitude | Global Z Vel | Kalman Global Z Accel
3679 | -0.30000001192092896 | -0.009999999776482582 | -0.0 | 0.3125 | 271.125 | 360.0 | -0.2999432682991028 | 57.625 | 3.0 | 3.0 | 3 | 57.625 | 10.0 | -0.2999432682991028
4203 | -0.30000001192092896 | -0.009999999776482582 | -0.0 | 0.3125 | 271.125 | 360.0 | -0.2999432682991028 | 57.875 | 3.0 | 3.0 | 3 | -0.31254586577415466 | 0.0 | 0.0
4726 | -0.3100000023841858 | -0.0 | -0.0 | 0.3125 | 271.125 | 360.0 | -0.30994027853012085 | 57.625 | 3.0 | 3.0 | 3 | -0.34453269839286804 | 0.0 | 0.0
5250 | -0.3199999928474426 | -0.0 | -0.0 | 0.3125 | 271.125 | 360.0 | -0.3199383318424225 | 57.875 | 3.0 | 3.0 | 3 | -0.3642825186252594 | 0.0 | 0.0
5774 | -0.3199999928474426 | -0.0 | -0.019999999552965164 | 0.3125 | 271.125 | 360.0 | -0.3203309178352356 | 57.875 | 3.0 | 3.0 | 3 | -0.3653147518634796 | 0.0 | 0.0
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

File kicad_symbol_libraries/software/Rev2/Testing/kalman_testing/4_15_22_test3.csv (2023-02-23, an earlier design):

Time since launch (ms) | X Acceleration (m/s) | Y Acceleration (m/s) | Z Acceleration (m/s) | X Orientation | Y Orientation | Z Orientation | Global Z Accel | Altitude (m) | Latitude | Longitude | Phase | Kalman Altitude | Global Z Vel | Kalman Global Z Accel
2809 | -0.28999999165534973 | 0.009999999776482582 | -0.0 | 0.3125 | 271.5625 | 0.125 | -0.28989070653915405 | 58.6875 | 3.0 | 3.0 | 3 | 58.6875 | 10.0 | -0.28989070653915405
3333 | -0.3100000023841858 | -0.0 | -0.009999999776482582 | 0.3125 | 271.5625 | 0.125 | -0.3101573884487152 | 59.3125 | 3.0 | 3.0 | 3 | 61.433902740478516 | 9.611441612243652 | -0.31370043754577637
3856 | -0.33000001311302185 | 0.029999999329447746 | -0.029999999329447746 | 0.3125 | 271.5625 | 0.125 | -0.33069077134132385 | 59.1875 | 3.0 | 3.0 | 3 | 62.008514404296875 | 8.352315902709961 | -0.3564586937427521
4380 | -0.33000001311302185 | -0.0 | -0.0 | 0.3125 | 271.5625 | 0.125 | -0.3298773467540741 | 59.1875 | 3.0 | 3.0 | 3 | 61.69854736328125 | 6.434121608734131 | -0.3758251667022705
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

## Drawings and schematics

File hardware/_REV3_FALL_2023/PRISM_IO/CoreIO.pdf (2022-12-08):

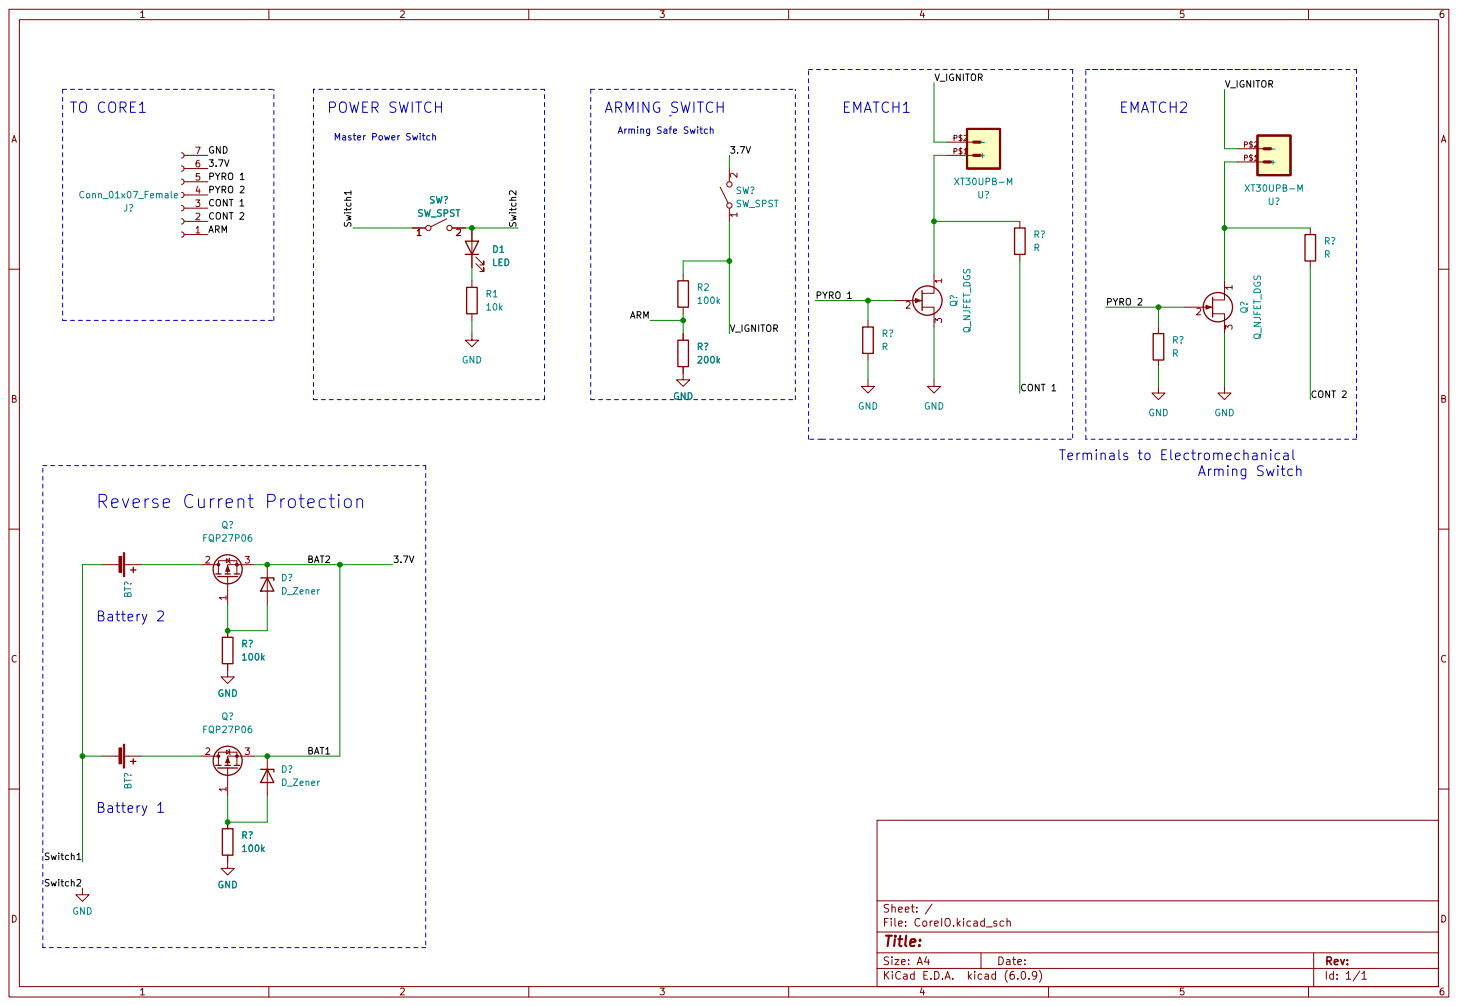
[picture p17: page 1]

Master Power Switch Battery 2

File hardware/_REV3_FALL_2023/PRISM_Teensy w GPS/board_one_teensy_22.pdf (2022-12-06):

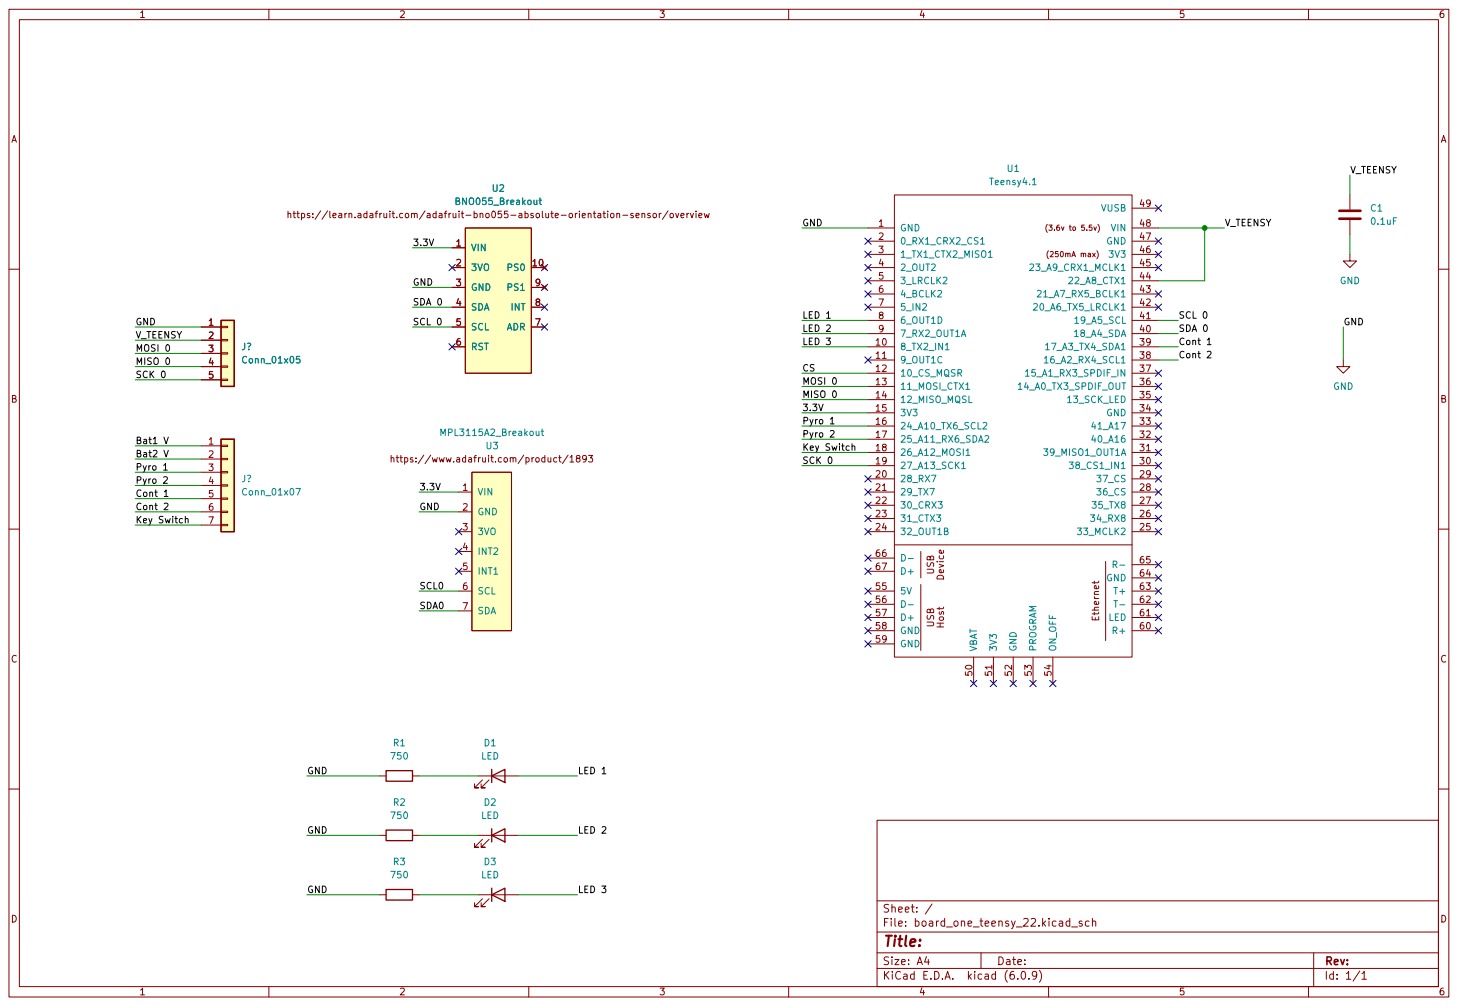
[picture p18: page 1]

https://learn.adafruit.com/adafruit-bno055-absolute-orientation-sensor/overview

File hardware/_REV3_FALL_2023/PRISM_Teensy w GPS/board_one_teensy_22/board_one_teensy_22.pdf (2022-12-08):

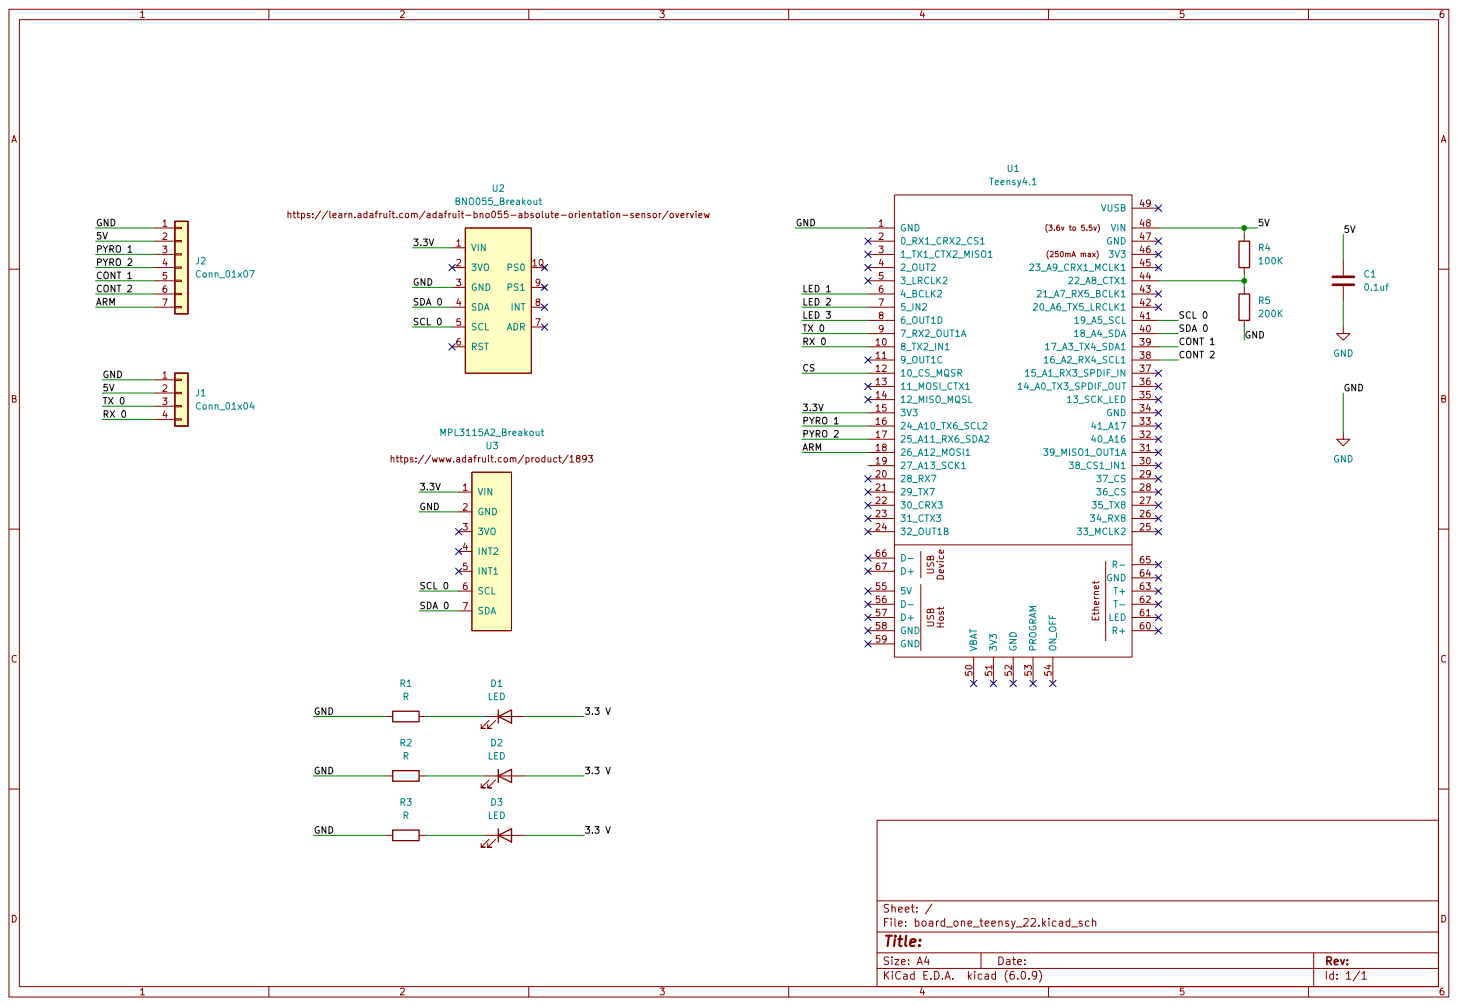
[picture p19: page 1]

5V CONT 2 SCL 0 CONT 1 SDA 0

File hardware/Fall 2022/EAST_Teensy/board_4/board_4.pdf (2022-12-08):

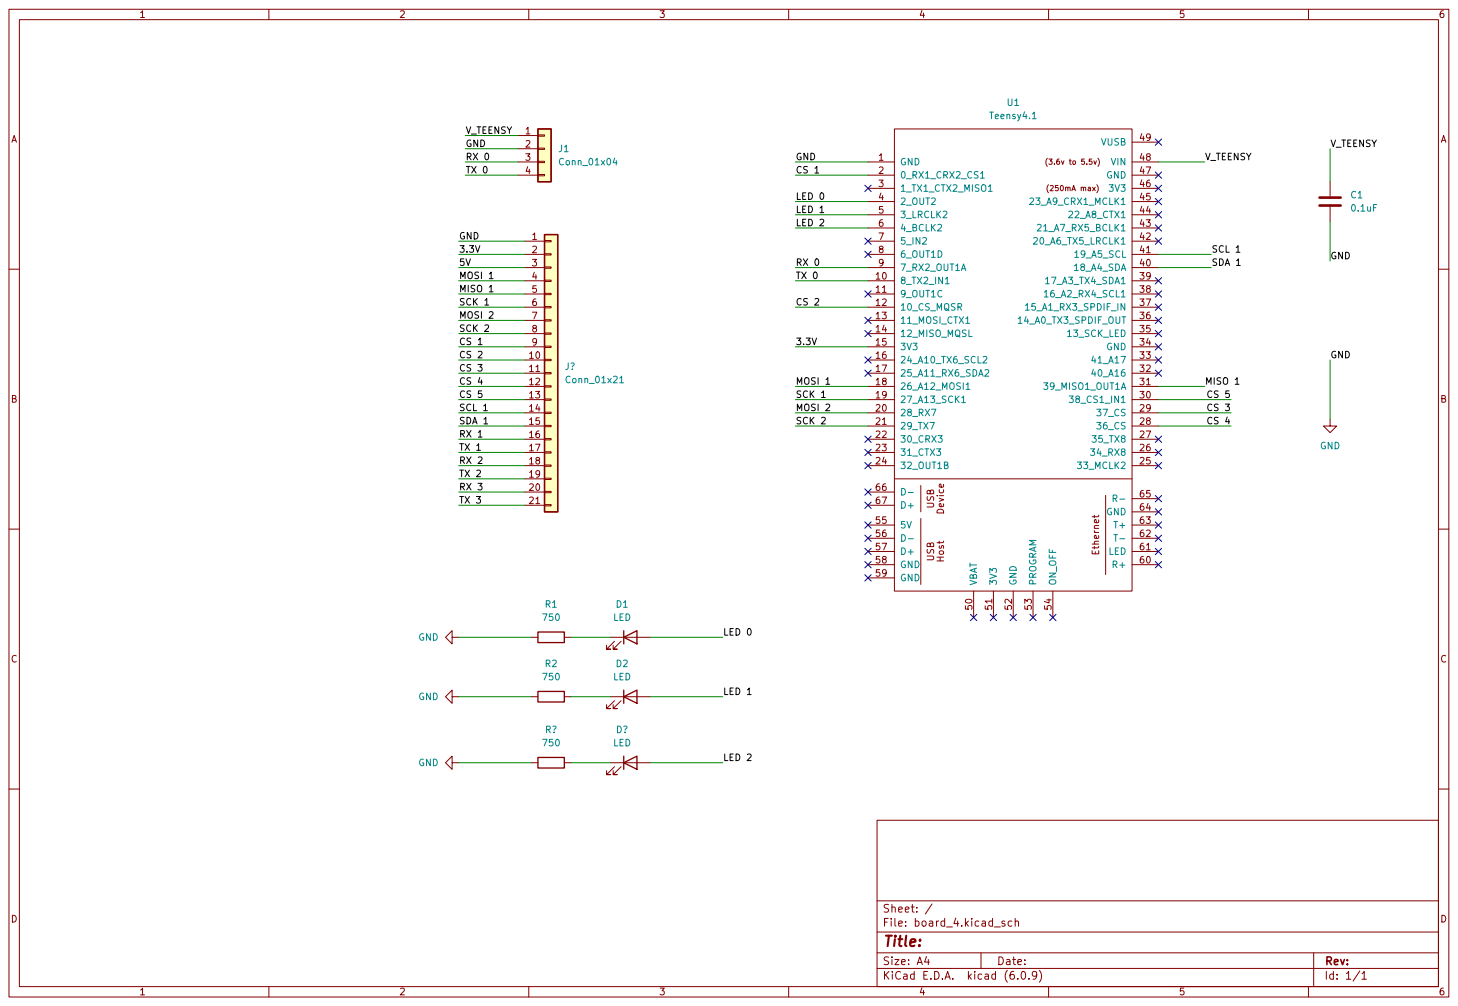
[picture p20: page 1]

GND
LED 0 MOSI 1 SCK 1 CS 2 RX 0 TX 0
LED 1

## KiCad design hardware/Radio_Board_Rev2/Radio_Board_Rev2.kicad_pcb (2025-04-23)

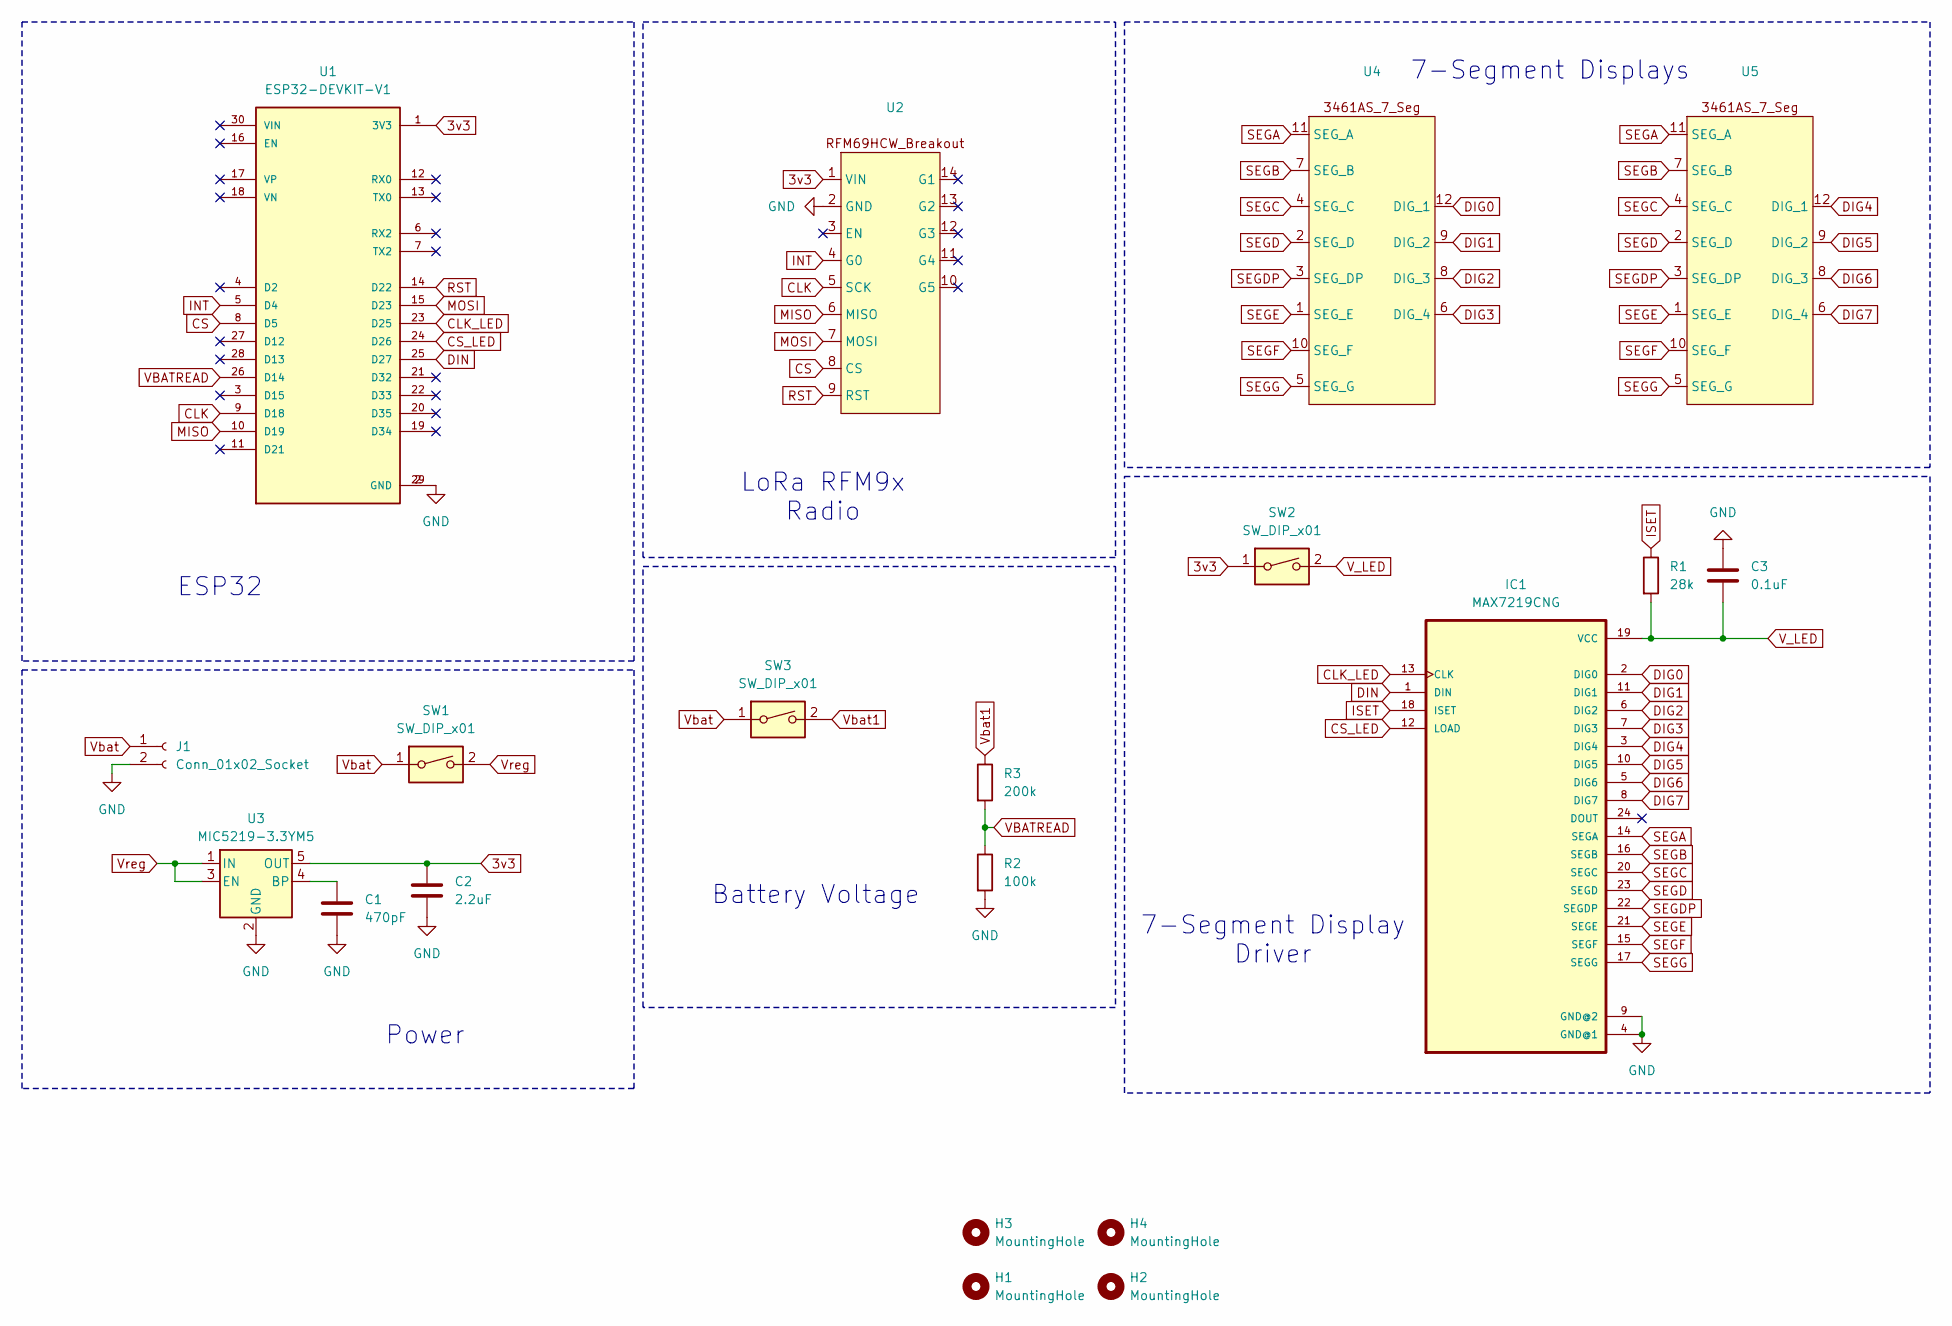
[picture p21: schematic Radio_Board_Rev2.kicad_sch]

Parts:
C1: 470pF; C_0603_1608Metric_Pad1.08x0.95mm_HandSolder
C2: 2.2uF; C_0603_1608Metric_Pad1.08x0.95mm_HandSolder
C3: 0.1uF; C_0603_1608Metric_Pad1.08x0.95mm_HandSolder
H1, H2, H3, H4: MountingHole; MountingHole_3.2mm_M3_DIN965_Pad_TopBottom
IC1: MAX7219CNG; DIP794W47P254L3213H457Q24
J1: Conn_01x02_Socket; JST_XH_B2B-XH-A_1x02_P2.50mm_Vertical
R1: 28k; R_0603_1608Metric_Pad0.98x0.95mm_HandSolder
R2: 100k; R_0603_1608Metric_Pad0.98x0.95mm_HandSolder
R3: 200k; R_0603_1608Metric_Pad0.98x0.95mm_HandSolder
SW1, SW2, SW3: SW_DIP_x01; PinSocket_1x02_P2.54mm_Vertical
U1: ESP32-DEVKIT-V1; MODULE_ESP32_DEVKIT_V1; PARTREV N/A
U2: RFM69HCW_Breakout
U3: MIC5219-3.3YM5; SOT-23-5
U4, U5: 3461AS_7_seg

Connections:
3v3: C2.1, SW2.1, U1.1 (3V3), U2.1 (VIN), U3.5 (OUT)
CLK: U1.9 (D18), U2.5 (SCK)
CLK_LED: IC1.13 (CLK), U1.23 (D25)
CS: U1.8 (D5), U2.8 (CS)
CS_LED: IC1.12 (LOAD), U1.24 (D26)
DIG0: IC1.2 (DIG0), U4.12 (DIG_1); also elsewhere on the board
DIG1: IC1.11 (DIG1), U4.9 (DIG_2); also elsewhere on the board
DIG2: IC1.6 (DIG2), U4.8 (DIG_3); also elsewhere on the board
DIG3: IC1.7 (DIG3), U4.6 (DIG_4); also elsewhere on the board
DIG4: IC1.3 (DIG4), U5.12 (DIG_1); also elsewhere on the board
DIG5: IC1.10 (DIG5), U5.9 (DIG_2); also elsewhere on the board
DIG6: IC1.5 (DIG6), U5.8 (DIG_3); also elsewhere on the board
DIG7: IC1.8 (DIG7), U5.6 (DIG_4); also elsewhere on the board
DIN: IC1.1 (DIN), U1.25 (D27)
GND: C1.2, C2.2, C3.1, IC1.4 (GND@1), IC1.9 (GND@2), J1.2, R2.2, U1.2 (GND), U1.29 (GND), U2.2 (GND), U3.2 (GND)
INT: U1.5 (D4), U2.4 (G0)
ISET: IC1.18 (ISET), R1.1
MISO: U1.10 (D19), U2.6 (MISO)
MOSI: U1.15 (D23), U2.7 (MOSI)
unnamed: C1.1, U3.4 (BP)
RST: U1.14 (D22), U2.9 (RST)
SEGA: IC1.14 (SEGA), U4.11 (SEG_A), U5.11 (SEG_A); also elsewhere on the board
SEGB: IC1.16 (SEGB), U4.7 (SEG_B), U5.7 (SEG_B); also elsewhere on the board
SEGC: IC1.20 (SEGC), U4.4 (SEG_C), U5.4 (SEG_C); also elsewhere on the board
SEGD: IC1.23 (SEGD), U4.2 (SEG_D), U5.2 (SEG_D); also elsewhere on the board
SEGDP: IC1.22 (SEGDP), U4.3 (SEG_DP), U5.3 (SEG_DP); also elsewhere on the board
SEGE: IC1.21 (SEGE), U4.1 (SEG_E), U5.1 (SEG_E); also elsewhere on the board
SEGF: IC1.15 (SEGF), U4.10 (SEG_F), U5.10 (SEG_F); also elsewhere on the board
SEGG: IC1.17 (SEGG), U4.5 (SEG_G), U5.5 (SEG_G); also elsewhere on the board
VBATREAD: R2.1, R3.2, U1.26 (D14)
V_LED: C3.2, IC1.19 (VCC), R1.2, SW2.2
Vbat: J1.1, SW1.1, SW3.1
Vbat1: R3.1, SW3.2
Vreg: SW1.2, U3.1 (IN), U3.3 (EN)

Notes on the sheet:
Battery Voltage
Power
ESP32
7-Segment Display Driver
7-Segment Displays
LoRa RFM9x Radio

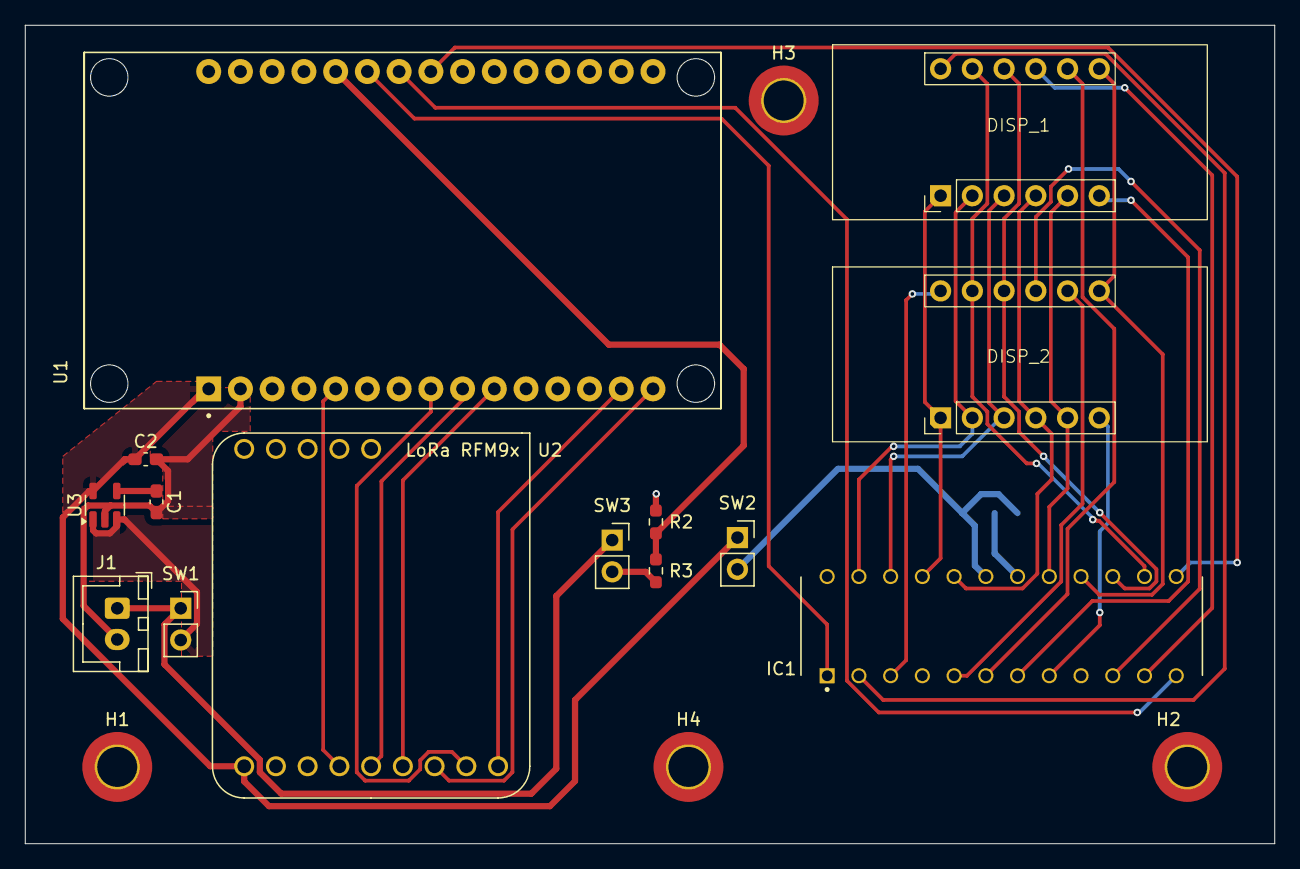
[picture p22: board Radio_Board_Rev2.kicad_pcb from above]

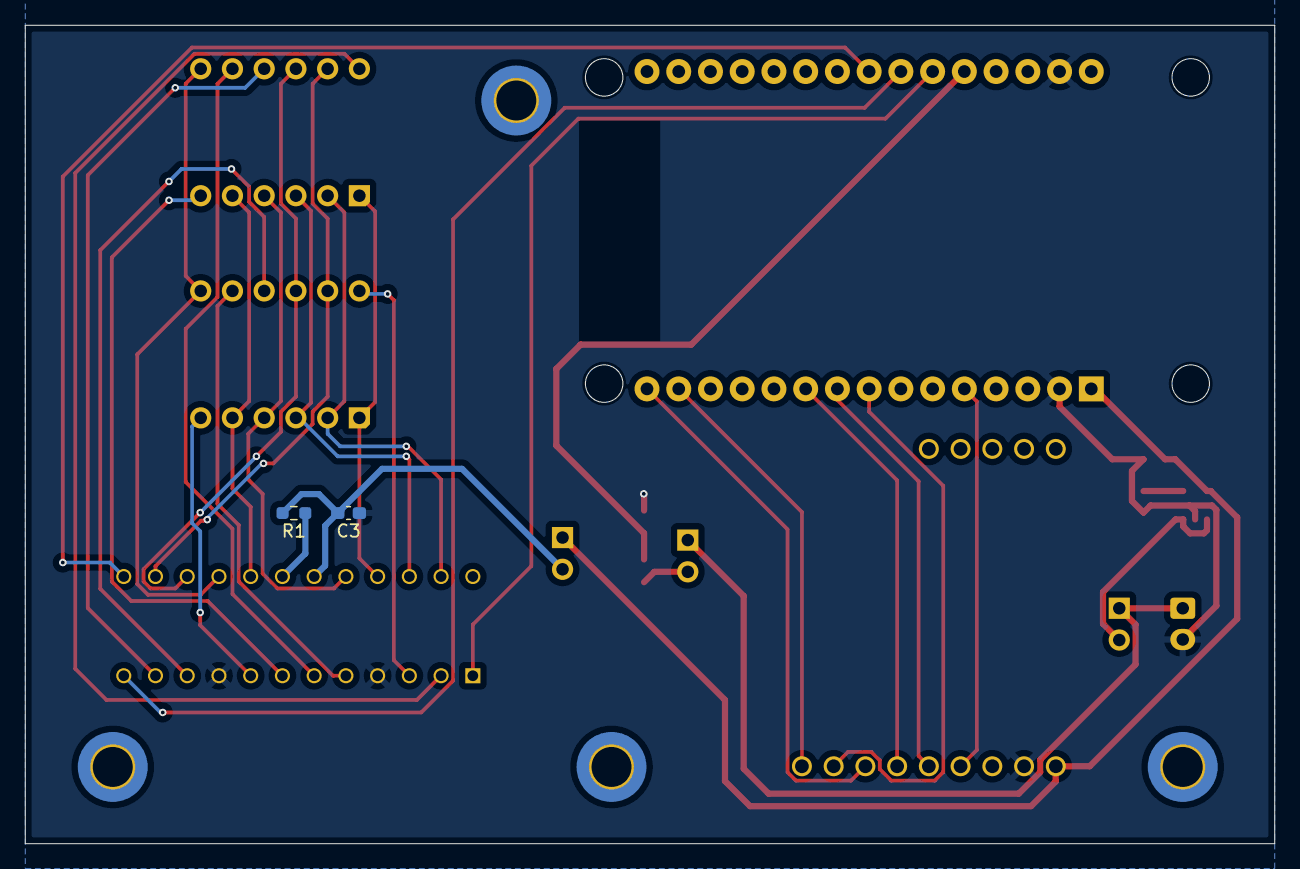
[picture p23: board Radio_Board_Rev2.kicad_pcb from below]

Board: 2 copper layers, 100.0 x 65.5 mm, 20 parts (2 on the bottom side), 34 nets.

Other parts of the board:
DISP_1, DISP_2: 3461AS_7_seg

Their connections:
DIG0: DISP_1.12 (DIG_1); also elsewhere on the board
DIG1: DISP_1.9 (DIG_2); also elsewhere on the board
DIG2: DISP_1.8 (DIG_3); also elsewhere on the board
DIG3: DISP_1.6 (DIG_4); also elsewhere on the board
DIG4: DISP_2.12 (DIG_1); also elsewhere on the board
DIG5: DISP_2.9 (DIG_2); also elsewhere on the board
DIG6: DISP_2.8 (DIG_3); also elsewhere on the board
DIG7: DISP_2.6 (DIG_4); also elsewhere on the board
SEGA: DISP_1.11 (SEG_A), DISP_2.11 (SEG_A); also elsewhere on the board
SEGB: DISP_1.7 (SEG_B), DISP_2.7 (SEG_B); also elsewhere on the board
SEGC: DISP_1.4 (SEG_C), DISP_2.4 (SEG_C); also elsewhere on the board
SEGD: DISP_1.2 (SEG_D), DISP_2.2 (SEG_D); also elsewhere on the board
SEGDP: DISP_1.3 (SEG_DP), DISP_2.3 (SEG_DP); also elsewhere on the board
SEGE: DISP_1.1 (SEG_E), DISP_2.1 (SEG_E); also elsewhere on the board
SEGF: DISP_1.10 (SEG_F), DISP_2.10 (SEG_F); also elsewhere on the board
SEGG: DISP_1.5 (SEG_G), DISP_2.5 (SEG_G); also elsewhere on the board

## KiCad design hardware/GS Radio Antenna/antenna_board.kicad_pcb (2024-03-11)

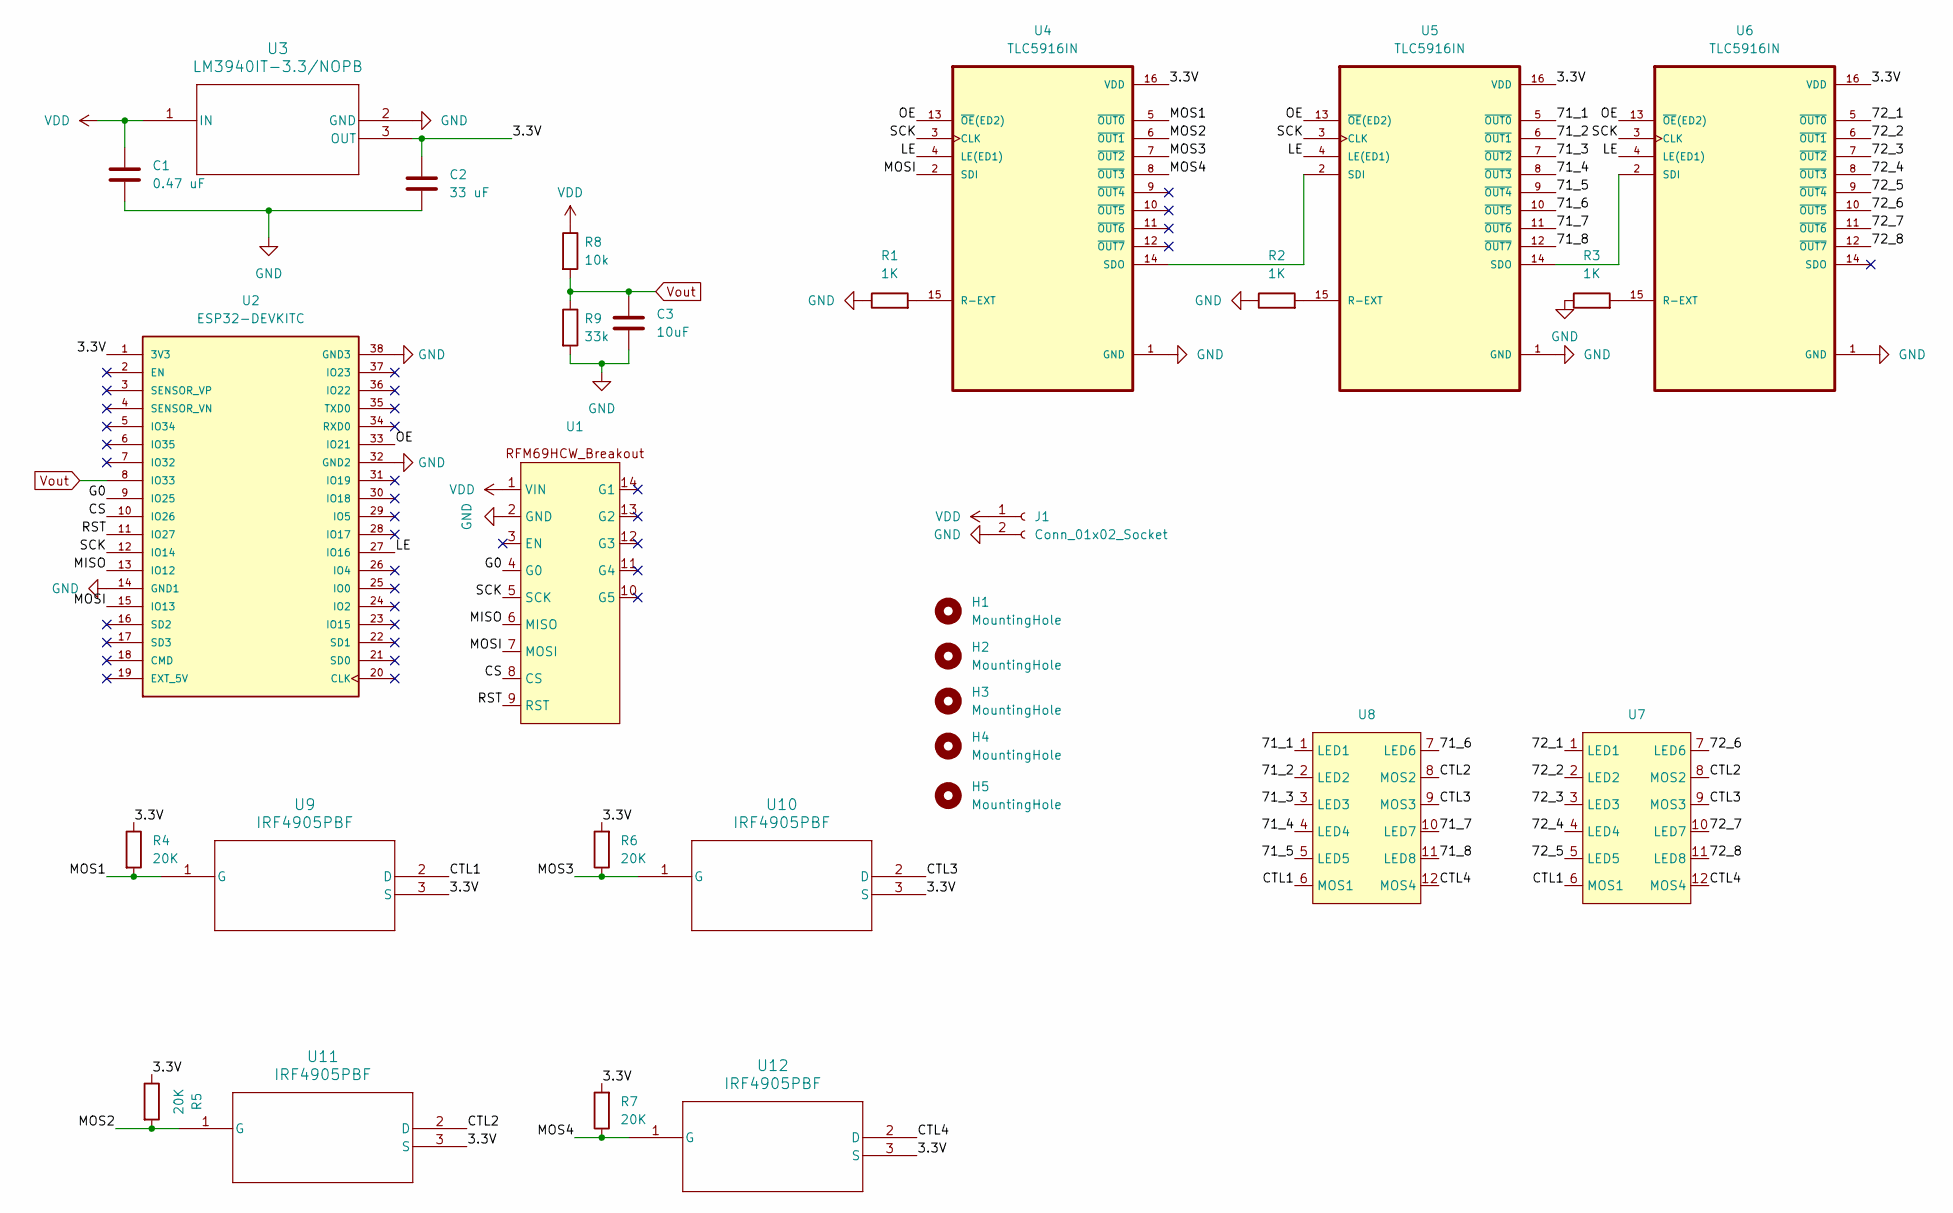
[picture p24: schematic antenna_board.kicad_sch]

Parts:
C1: 0.47 uF; C_0603_1608Metric_Pad1.08x0.95mm_HandSolder
C2: 33 uF; C_0805_2012Metric_Pad1.18x1.45mm_HandSolder
C3: 10uF; C_0603_1608Metric_Pad1.08x0.95mm_HandSolder
H1, H2, H3, H4, H5: MountingHole; MountingHole_3.2mm_M3_DIN965_Pad_TopBottom
J1: Conn_01x02_Socket; PinSocket_1x02_P2.54mm_Vertical
R1, R2, R3: 1K; R_0603_1608Metric_Pad0.98x0.95mm_HandSolder
R4, R5, R6, R7: 20K; R_0603_1608Metric_Pad0.98x0.95mm_HandSolder
R8: 10k; R_0603_1608Metric_Pad0.98x0.95mm_HandSolder
R9: 33k; R_0603_1608Metric_Pad0.98x0.95mm_HandSolder
U1: RFM69HCW_Breakout
U2: ESP32-DEVKITC; MODULE_ESP32-DEVKITC; PARTREV N/A
U3: LM3940IT-3.3/NOPB; LM3940IT
U4, U5, U6: TLC5916IN; DigiKey_Part_Number 296-24383-5-ND
U7, U8: Seven_Segment_Display
U9, U10, U11, U12: IRF4905PBF; PG-TO220-3_INF

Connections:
/3.3V: C2.1, R4.1, R5.1, R6.2, R7.2, U2.1 (3V3), U3.3 (OUT), U4.16 (VDD), U5.16 (VDD), U6.16 (VDD), U9.3 (S), U10.3 (S), U11.3 (S), U12.3 (S)
/71_1: U5.5 (~OUT0), U8.1 (LED1)
/71_2: U5.6 (~OUT1), U8.2 (LED2)
/71_3: U5.7 (~OUT2), U8.3 (LED3)
/71_4: U5.8 (~OUT3), U8.4 (LED4)
/71_5: U5.9 (~OUT4), U8.5 (LED5)
/71_6: U5.10 (~OUT5), U8.7 (LED6)
/71_7: U5.11 (~OUT6), U8.10 (LED7)
/71_8: U5.12 (~OUT7), U8.11 (LED8)
/72_1: U6.5 (~OUT0), U7.1 (LED1)
/72_2: U6.6 (~OUT1), U7.2 (LED2)
/72_3: U6.7 (~OUT2), U7.3 (LED3)
/72_4: U6.8 (~OUT3), U7.4 (LED4)
/72_5: U6.9 (~OUT4), U7.5 (LED5)
/72_6: U6.10 (~OUT5), U7.7 (LED6)
/72_7: U6.11 (~OUT6), U7.10 (LED7)
/72_8: U6.12 (~OUT7), U7.11 (LED8)
/CS: U1.8 (CS), U2.10 (IO26)
/CTL1: U7.6 (MOS1), U8.6 (MOS1), U9.2 (D)
/CTL2: U7.8 (MOS2), U8.8 (MOS2), U11.2 (D)
/CTL3: U7.9 (MOS3), U8.9 (MOS3), U10.2 (D)
/CTL4: U7.12 (MOS4), U8.12 (MOS4), U12.2 (D)
/G0: U1.4 (G0), U2.9 (IO25)
/LE: U2.27 (IO16), U4.4 (LE(ED1)), U5.4 (LE(ED1)), U6.4 (LE(ED1))
/MISO: U1.6 (MISO), U2.13 (IO12)
/MOS1: R4.2, U4.5 (~OUT0), U9.1 (G)
/MOS2: R5.2, U4.6 (~OUT1), U11.1 (G)
/MOS3: R6.1, U4.7 (~OUT2), U10.1 (G)
/MOS4: R7.1, U4.8 (~OUT3), U12.1 (G)
/MOSI: U1.7 (MOSI), U2.15 (IO13), U4.2 (SDI)
/OE: U2.33 (IO21), U4.13 (~OE(ED2)), U5.13 (~OE(ED2)), U6.13 (~OE(ED2))
/RST: U1.9 (RST), U2.11 (IO27)
/SCK: U1.5 (SCK), U2.12 (IO14), U4.3 (CLK), U5.3 (CLK), U6.3 (CLK)
GND: C1.2, C2.2, C3.2, J1.2, R1.1, R2.1, R3.1, R9.2, U1.2 (GND), U2.14 (GND1), U2.32 (GND2), U2.38 (GND3), U3.2 (GND), U4.1 (GND), U5.1 (GND), U6.1 (GND)
unnamed: R1.2, U4.15 (R-EXT)
unnamed: U4.14 (SDO), U5.2 (SDI)
unnamed: R2.2, U5.15 (R-EXT)
unnamed: U5.14 (SDO), U6.2 (SDI)
unnamed: R3.2, U6.15 (R-EXT)
VDD: C1.1, J1.1, R8.1, U1.1 (VIN), U3.1 (IN)
Vout: C3.1, R8.2, R9.1, U2.8 (IO33)

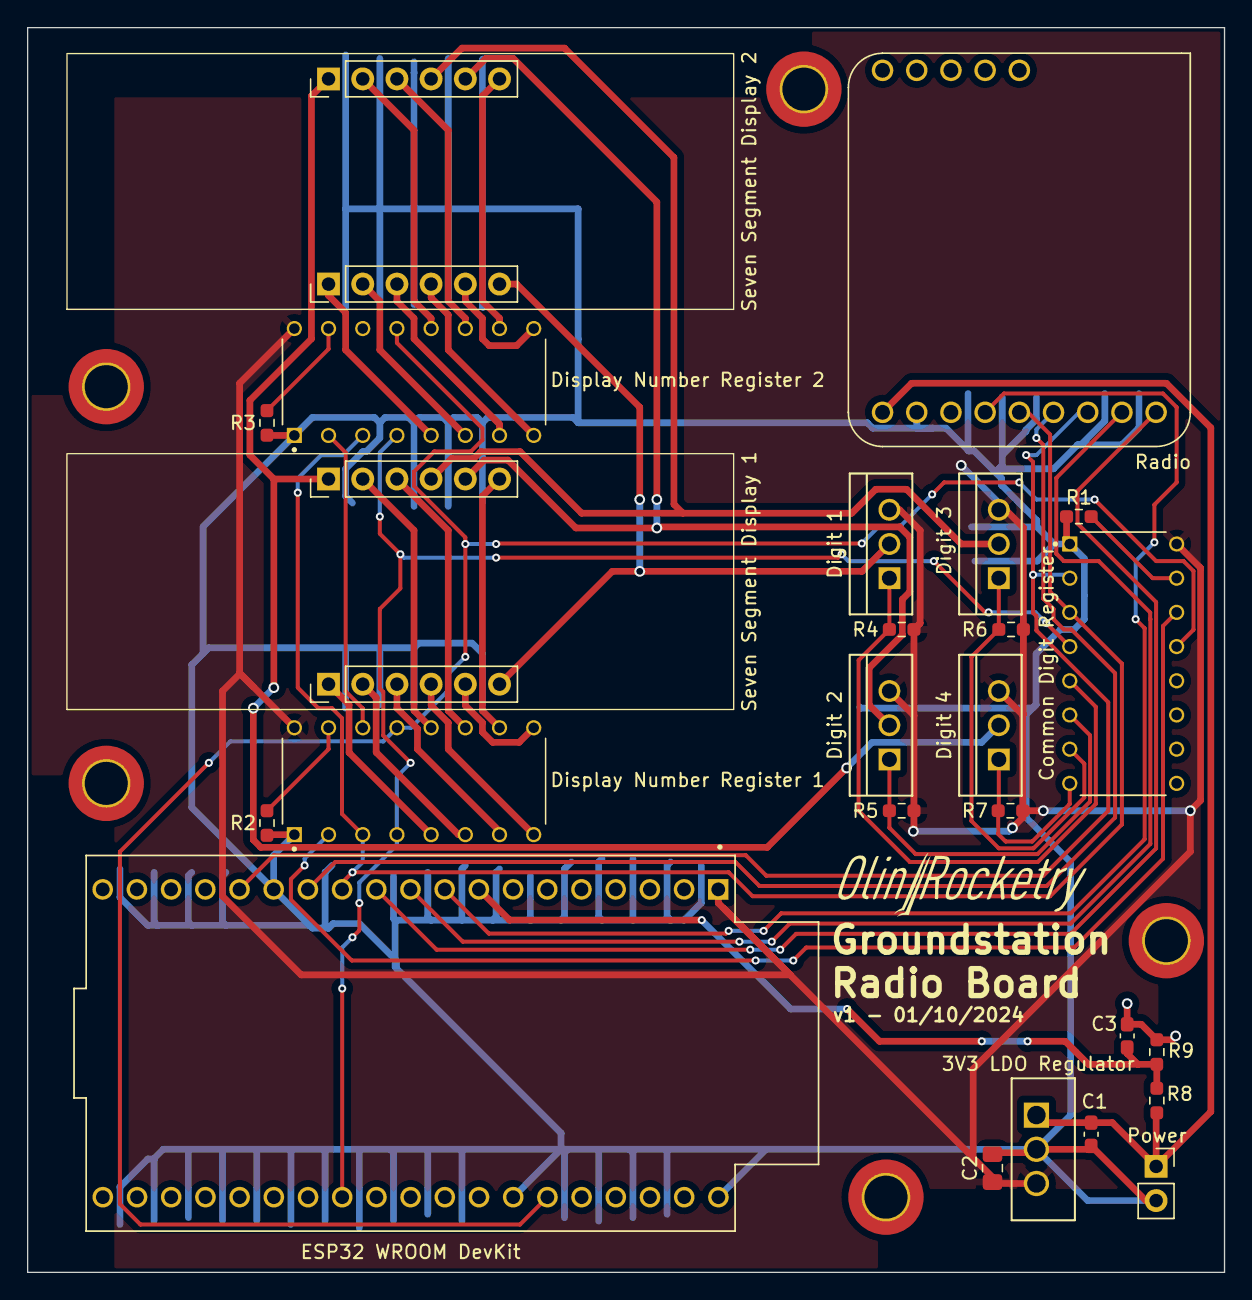
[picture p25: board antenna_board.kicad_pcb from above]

Board: 2 copper layers, 88.9 x 92.5 mm, 30 parts (0 on the bottom side), 41 nets.

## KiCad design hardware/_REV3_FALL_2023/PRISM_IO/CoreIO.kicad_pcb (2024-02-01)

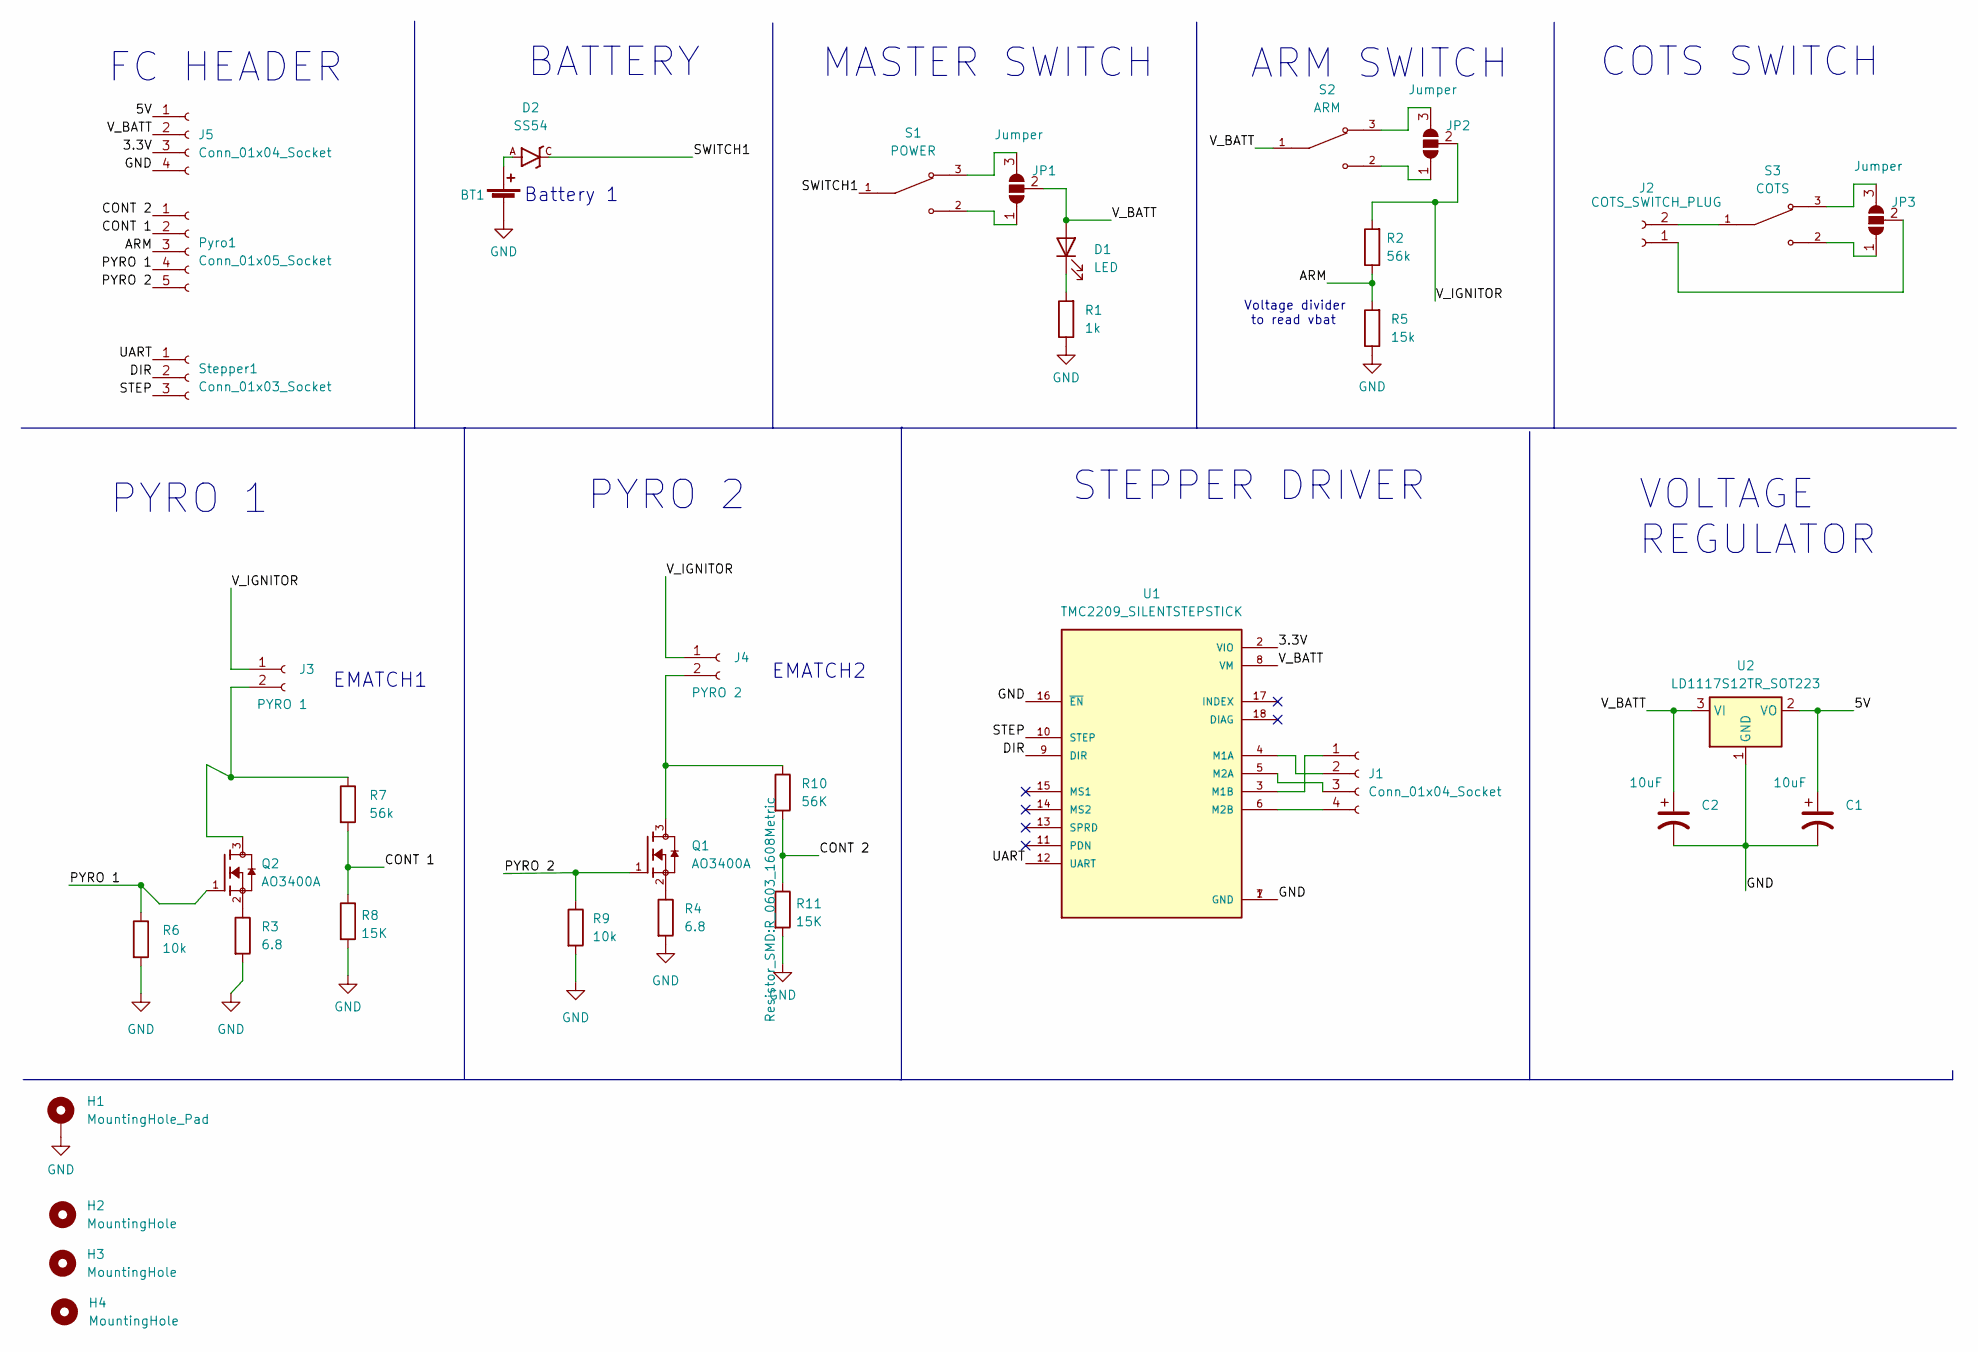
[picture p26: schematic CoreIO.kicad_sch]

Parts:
BT1: JST_XH_S02B-XH-A_02x2.50mm_Angled
C1, C2: 10uF; CP_EIA-3216-18_Kemet-A
D1: LED; LED_0603_1608Metric
D2: SS54; DO-214AC
H1: MountingHole_Pad; MountingHole_3.2mm_M3_DIN965_Pad_TopBottom
H2, H3, H4: MountingHole; MountingHole_3.2mm_M3_DIN965_Pad_TopBottom
J1: Conn_01x04_Socket; JST_XH_S04B-XH-A_04x2.50mm_Angled
J2: COTS_SWITCH_PLUG; JST_XH_S02B-XH-A_02x2.50mm_Angled
J3: PYRO 1; JST_XH_S02B-XH-A_02x2.50mm_Angled
J4: PYRO 2; JST_XH_S02B-XH-A_02x2.50mm_Angled
J5: Conn_01x04_Socket; PinHeader_1x04_P2.54mm_Vertical
JP1, JP2, JP3: Jumper; SolderJumper-3_P1.3mm_Open_Pad1.0x1.5mm_NumberLabels
Pyro1: Conn_01x05_Socket; PinHeader_1x05_P2.54mm_Vertical
Q1, Q2: AO3400A; SOT95P280X125-3N; PARTREV L
R1: 1k; R_0603_1608Metric
R2, R7: 56k; R_0603_1608Metric
R3, R4: 6.8; R_Axial_DIN0414_L11.9mm_D4.5mm_P15.24mm_Horizontal
R5: 15k; R_0603_1608Metric
R6, R9: 10k; R_0603_1608Metric
R8, R11: 15K; R_0603_1608Metric
R10: 56K; R_0603_1608Metric
S1: POWER; SW_D2F-01F; PARTREV B036-E1-12
S2: ARM; SW_D2F-01F; PARTREV B036-E1-12
S3: COTS; SW_D2F-01F; PARTREV B036-E1-12
Stepper1: Conn_01x03_Socket; PinHeader_1x03_P2.54mm_Vertical
U1: TMC2209_SILENTSTEPSTICK; MODULE_TMC2209_SILENTSTEPSTICK; PARTREV 1.20
U2: LD1117S12TR_SOT223; SOT-223-3_TabPin2

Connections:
/3.3V: J5.3, U1.2 (VIO)
/5V: C1.1, J5.1, U2.2 (VO)
/ARM: R2.1, R5.2; also elsewhere on the board
/CONT 1: R7.2, R8.1; also elsewhere on the board
/CONT 2: R10.2, R11.1; also elsewhere on the board
/DIR: U1.9 (DIR); also elsewhere on the board
/PYRO 1: Q2.1, R6.1; also elsewhere on the board
/PYRO 2: Q1.1, R9.1; also elsewhere on the board
/STEP: U1.10 (STEP); also elsewhere on the board
/SWITCH1: D2.C, S1.1
/UART: U1.12 (UART); also elsewhere on the board
/V_BATT: C2.1, D1.2 (A), J5.2, JP1.2 (C), S2.1, U1.8 (VM), U2.3 (VI)
/V_IGNITOR: J3.1, J4.1, JP2.2 (C), R2.2
GND: BT1.2 (-), C1.2, C2.2, H1.1, J5.4, R1.1, R3.2, R4.2, R5.1, R6.2, R8.2, R9.2, R11.2, U1.1 (GND), U1.7 (GND), U1.16 (~EN), U2.1 (GND)
unnamed: BT1.1 (+), D2.A
unnamed: D1.1 (K), R1.2
unnamed: J1.1, U1.3 (M1B)
unnamed: J1.2, U1.4 (M1A)
unnamed: J1.3, U1.5 (M2A)
unnamed: J1.4, U1.6 (M2B)
unnamed: J2.1, JP3.2 (C)
unnamed: J2.2, S3.1
unnamed: J3.2, Q2.3, R7.1
unnamed: J4.2, Q1.3, R10.1
unnamed: JP1.1 (A), S1.2
unnamed: JP1.3 (B), S1.3
unnamed: JP2.1 (A), S2.2
unnamed: JP2.3 (B), S2.3
unnamed: JP3.1 (A), S3.2
unnamed: JP3.3 (B), S3.3
unnamed: Q1.2, R4.1
unnamed: Q2.2, R3.1

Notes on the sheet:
ARM SWITCH
EMATCH1
PYRO 1
BATTERY
EMATCH2
Voltage divider to read vbat
VOLTAGE REGULATOR
MASTER SWITCH
PYRO 2
FC HEADER
STEPPER DRIVER
COTS SWITCH
Battery 1

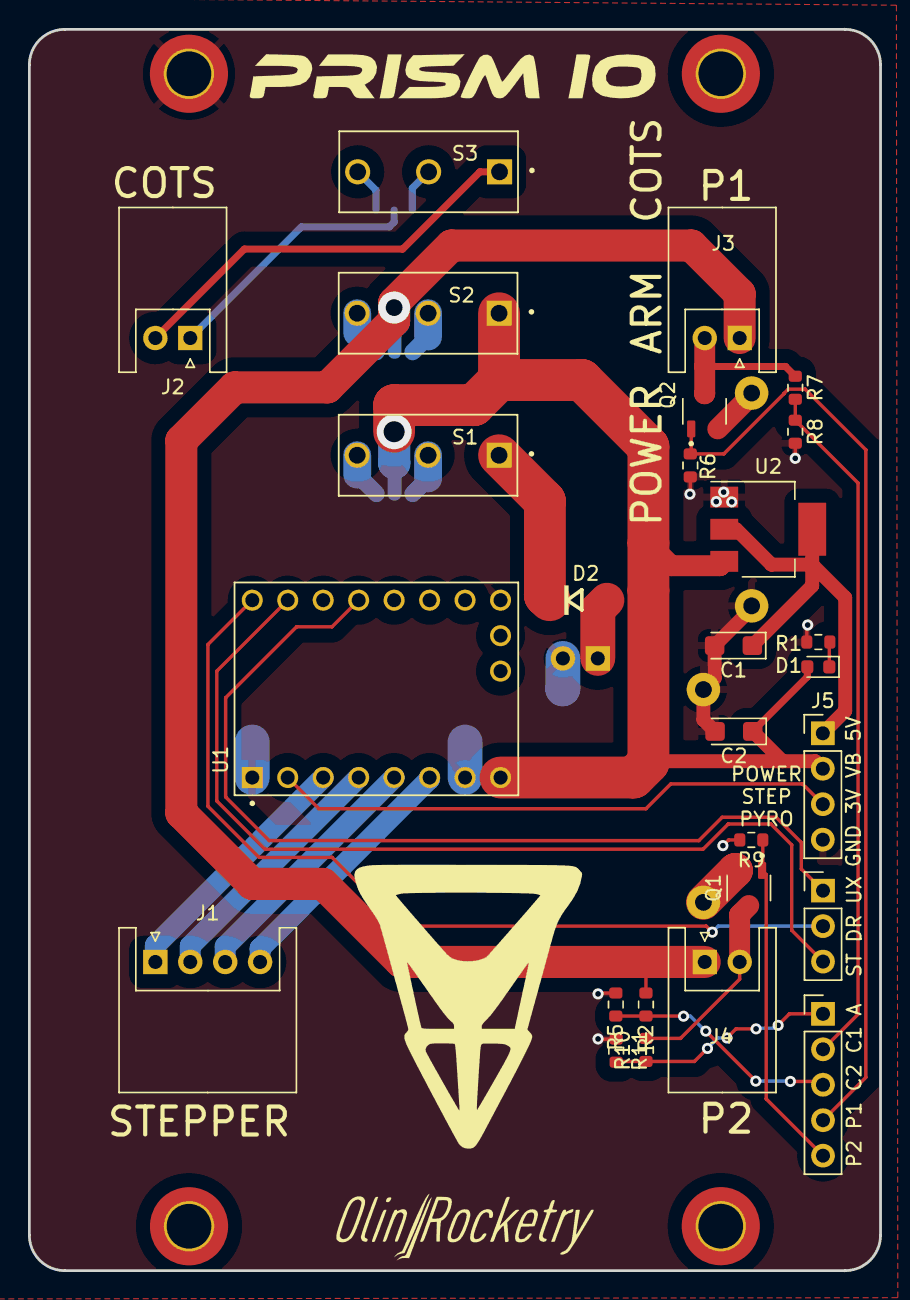
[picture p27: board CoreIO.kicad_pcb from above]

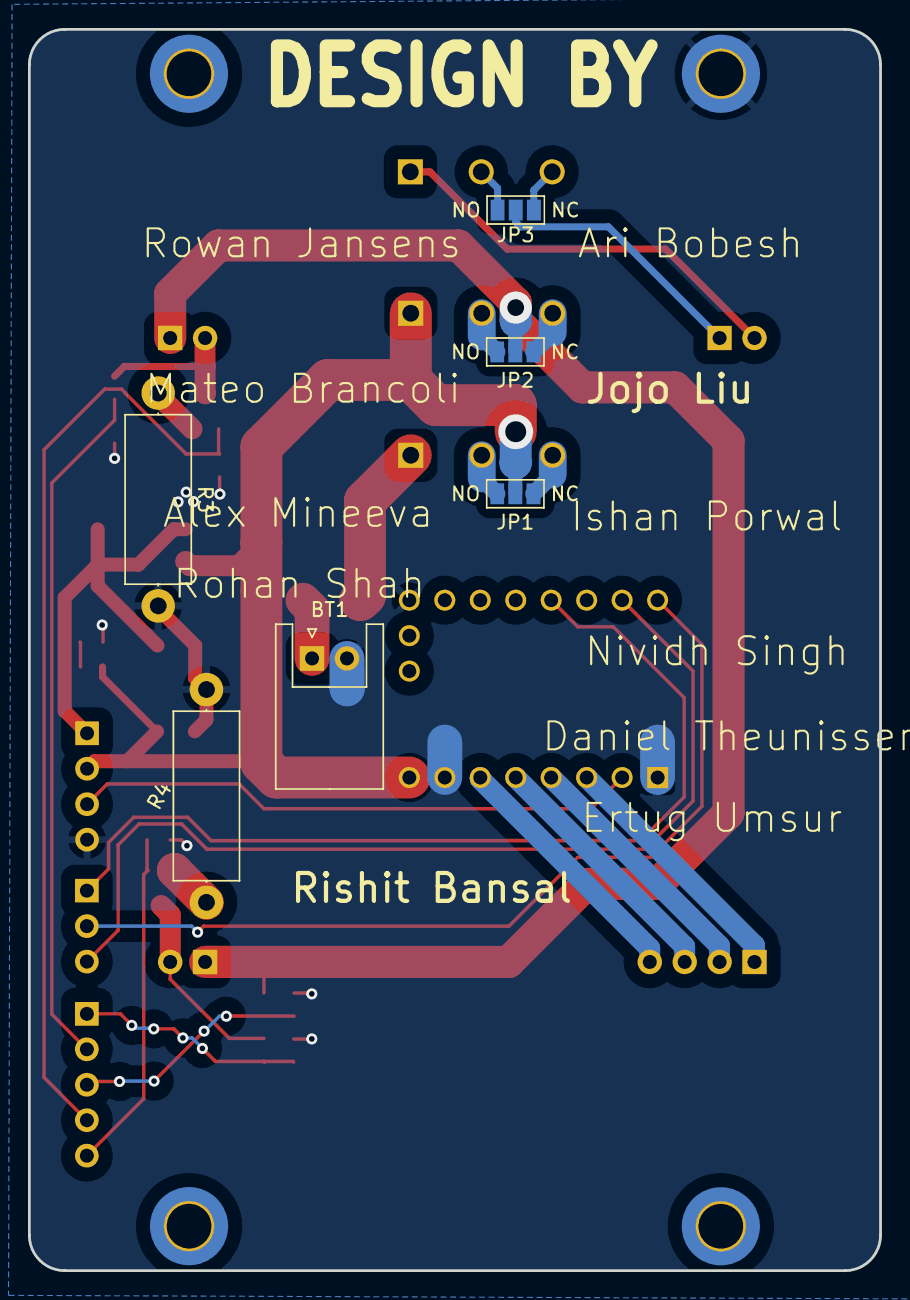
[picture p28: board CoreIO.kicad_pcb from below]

Board: 2 copper layers, 61.0 x 88.9 mm, 37 parts (6 on the bottom side), 32 nets.

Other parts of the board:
Pyro2: Conn_01x05_Socket; PinHeader_1x05_P2.54mm_Vertical
Stepper2: Conn_01x03_Socket; PinHeader_1x03_P2.54mm_Vertical

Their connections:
/ARM: Pyro2.3; also elsewhere on the board
/CONT 1: Pyro2.2; also elsewhere on the board
/CONT 2: Pyro2.1; also elsewhere on the board
/DIR: Stepper2.2; also elsewhere on the board
/PYRO 1: Pyro2.4; also elsewhere on the board
/PYRO 2: Pyro2.5; also elsewhere on the board
/STEP: Stepper2.3; also elsewhere on the board
/UART: Stepper2.1; also elsewhere on the board

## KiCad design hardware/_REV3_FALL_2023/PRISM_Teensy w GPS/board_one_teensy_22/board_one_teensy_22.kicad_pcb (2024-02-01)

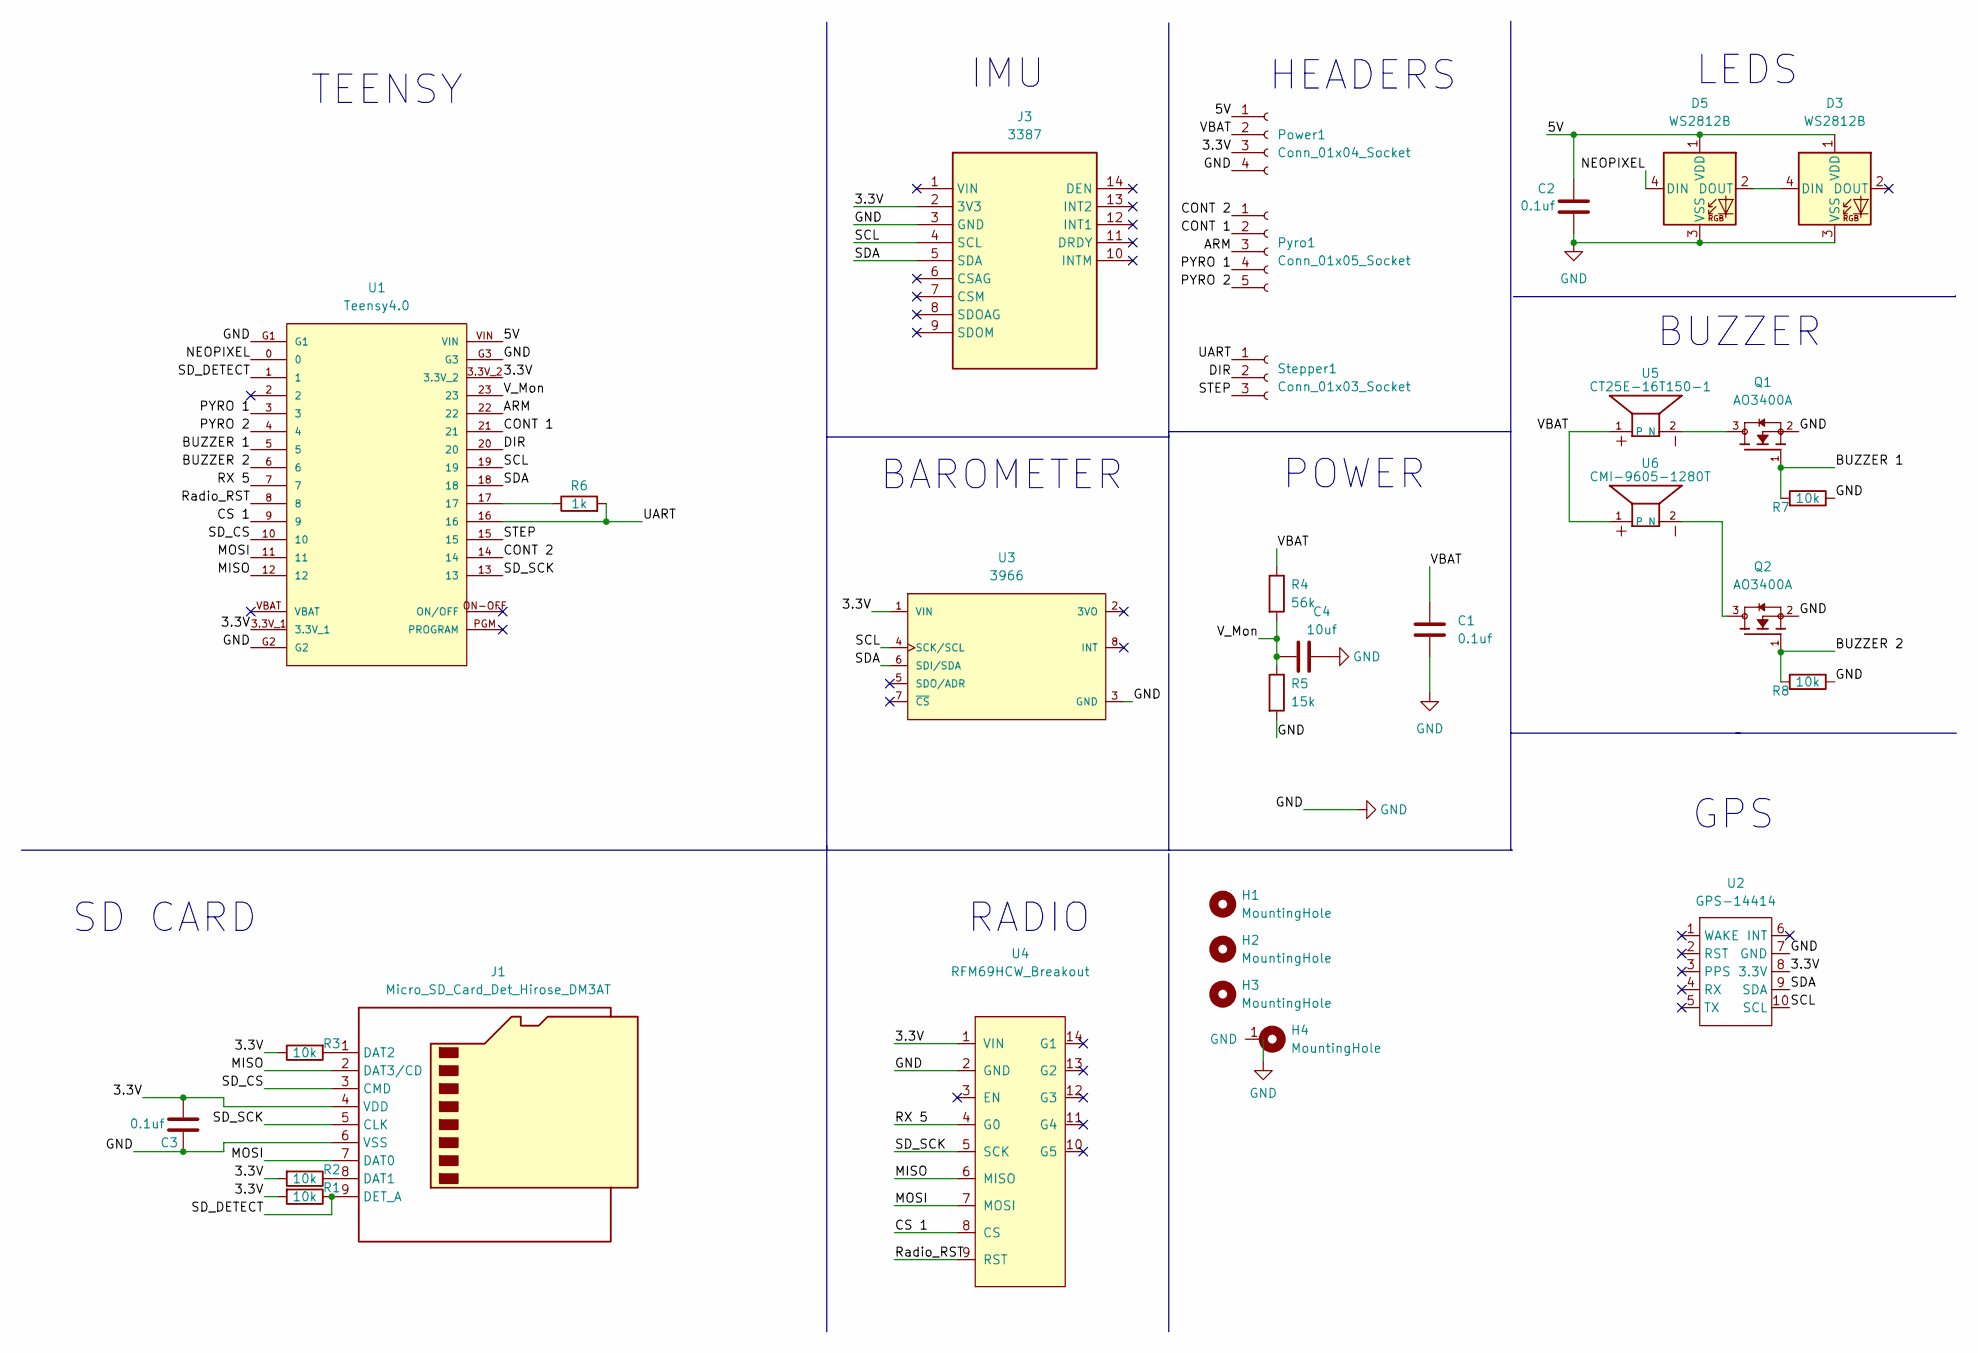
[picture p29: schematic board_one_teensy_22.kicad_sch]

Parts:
C1, C2, C3: 0.1uf; C_0603_1608Metric_Pad1.08x0.95mm_HandSolder
C4: 10uf; C_0603_1608Metric
D3, D5: WS2812B
H1, H2, H3, H4: MountingHole; MountingHole_3.2mm_M3_DIN965_Pad_TopBottom
J1: Micro_SD_Card_Det_Hirose_DM3AT; HRS_DM3CS-SF
J3: 3387; IMU MIni; Manufacturer_Part_Number 3387
Power1: Conn_01x04_Socket; PinHeader_1x04_P2.54mm_Vertical
Pyro1: Conn_01x05_Socket; PinHeader_1x05_P2.54mm_Vertical
Q1, Q2: AO3400A; SOT95P280X125-3N; PARTREV L
R1, R2, R3, R7, R8: 10k; R_0603_1608Metric_Pad0.98x0.95mm_HandSolder
R4: 56k; R_0603_1608Metric_Pad0.98x0.95mm_HandSolder
R5: 15k; R_0603_1608Metric_Pad0.98x0.95mm_HandSolder
R6: 1k; R_0603_1608Metric_Pad0.98x0.95mm_HandSolder
Stepper1: Conn_01x03_Socket; PinHeader_1x03_P2.54mm_Vertical
U1: Teensy4.0; MODULE_DEV-15583
U2: GPS-14414
U3: 3966; Adafruit_Industries-3966-MFG; mouser part number 485-3966; digikey description BMP388 - PRECISION BAROMETRIC PR
U4: RFM69HCW_Breakout
U5: CT25E-16T150-1; PARTREV 31/03/20
U6: CMI-9605-1280T; PARTREV 31/03/20

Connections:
/3.3V: C3.2, J1.4 (VDD), J3.2 (3V3), Power1.3, R1.2, R2.2, R3.1, U1.3.3V_1, U1.3.3V_2, U2.8 (3.3V), U3.1 (VIN), U4.1 (VIN)
/5V: C2.2, D3.1 (VDD), D5.1 (VDD), Power1.1, U1.VIN
/ARM: Pyro1.3, U1.22
/BUZZER 1: Q1.1, R7.2, U1.5
/BUZZER 2: Q2.1, R8.2, U1.6
/CONT 1: Pyro1.2, U1.21
/CONT 2: Pyro1.1, U1.14
/CS 1: U1.9, U4.8 (CS)
/DIR: Stepper1.2, U1.20
/MISO: J1.2 (DAT3/CD), U1.12, U4.6 (MISO)
/MOSI: J1.7 (DAT0), U1.11, U4.7 (MOSI)
/NEOPIXEL: D5.4 (DIN), U1.0
/PYRO 1: Pyro1.4, U1.3
/PYRO 2: Pyro1.5, U1.4
/RX 5: U1.7, U4.4 (G0)
/Radio_RST: U1.8, U4.9 (RST)
/SCL: J3.4 (SCL), U1.19, U2.10 (SCL), U3.4 (SCK/SCL)
/SDA: J3.5 (SDA), U1.18, U2.9 (SDA), U3.6 (SDI/SDA)
/SD_CS: J1.3 (CMD), U1.10
/SD_DETECT: J1.9 (DET_A), R1.1, U1.1
/SD_SCK: J1.5 (CLK), U1.13, U4.5 (SCK)
/STEP: Stepper1.3, U1.15
/UART: R6.2, Stepper1.1, U1.16
/VBAT: C1.1, Power1.2, R4.1, U5.1, U6.1
/V_Mon: C4.2, R4.2, R5.1, U1.23
GND: C1.2, C2.1, C3.1, C4.1, D3.3 (VSS), D5.3 (VSS), H4.1 (GND), J1.6 (VSS), J3.3 (GND), Power1.4, Q1.2, Q2.2, R5.2, R7.1, R8.1, U1.G1, U1.G2, U1.G3, U2.7 (GND), U3.3 (GND), U4.2 (GND)
unnamed: D3.4 (DIN), D5.2 (DOUT)
unnamed: J1.8 (DAT1), R2.1
unnamed: J1.1 (DAT2), R3.2
unnamed: R6.1, U1.17
unnamed: Q1.3, U5.2 (N)
unnamed: Q2.3, U6.2 (N)

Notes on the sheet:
BUZZER
TEENSY
HEADERS
SD CARD
POWER
LEDS
GPS
IMU
BAROMETER
RADIO

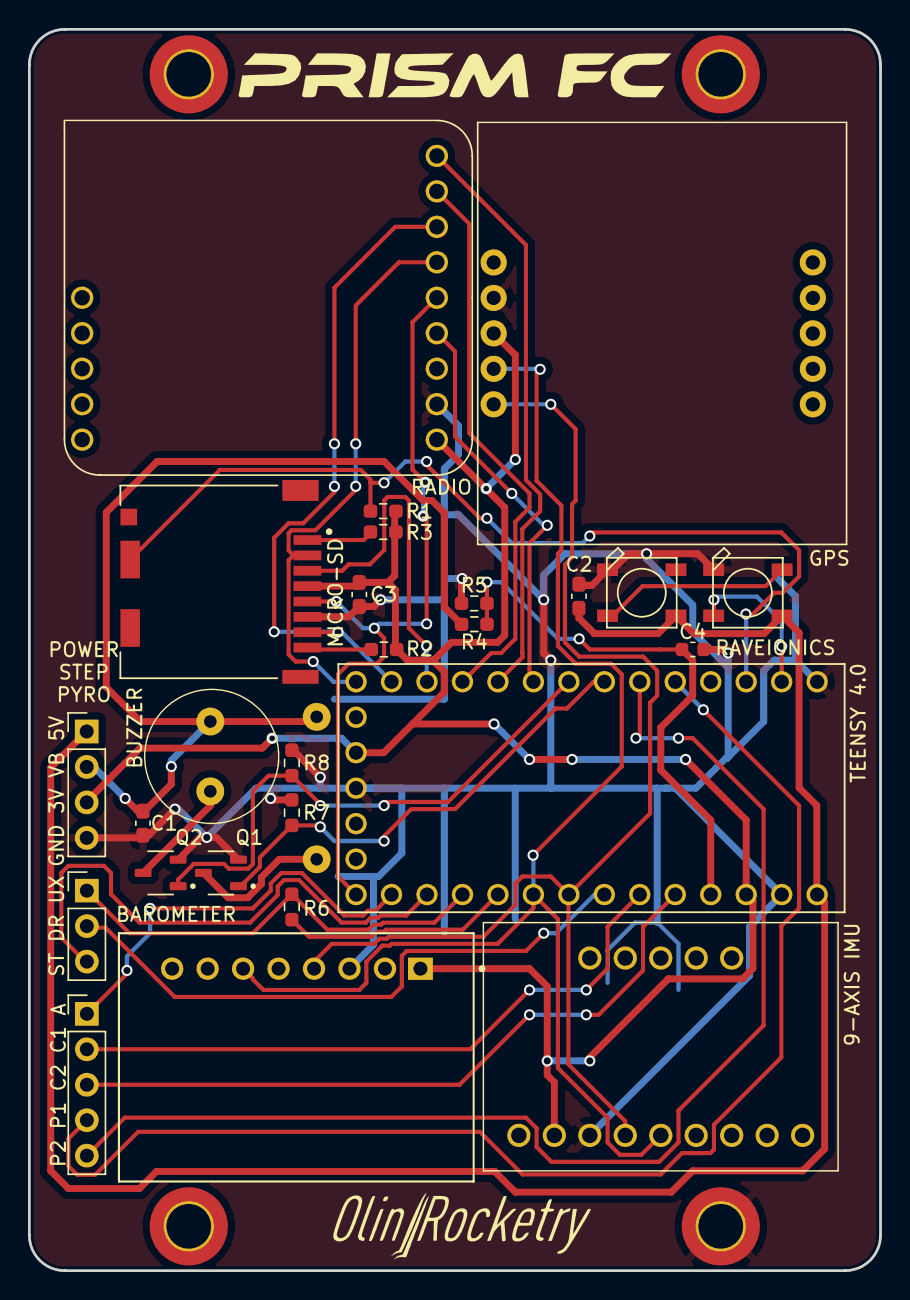
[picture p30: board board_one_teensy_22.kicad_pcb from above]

Board: 2 copper layers, 61.0 x 88.9 mm, 31 parts (1 on the bottom side), 32 nets.

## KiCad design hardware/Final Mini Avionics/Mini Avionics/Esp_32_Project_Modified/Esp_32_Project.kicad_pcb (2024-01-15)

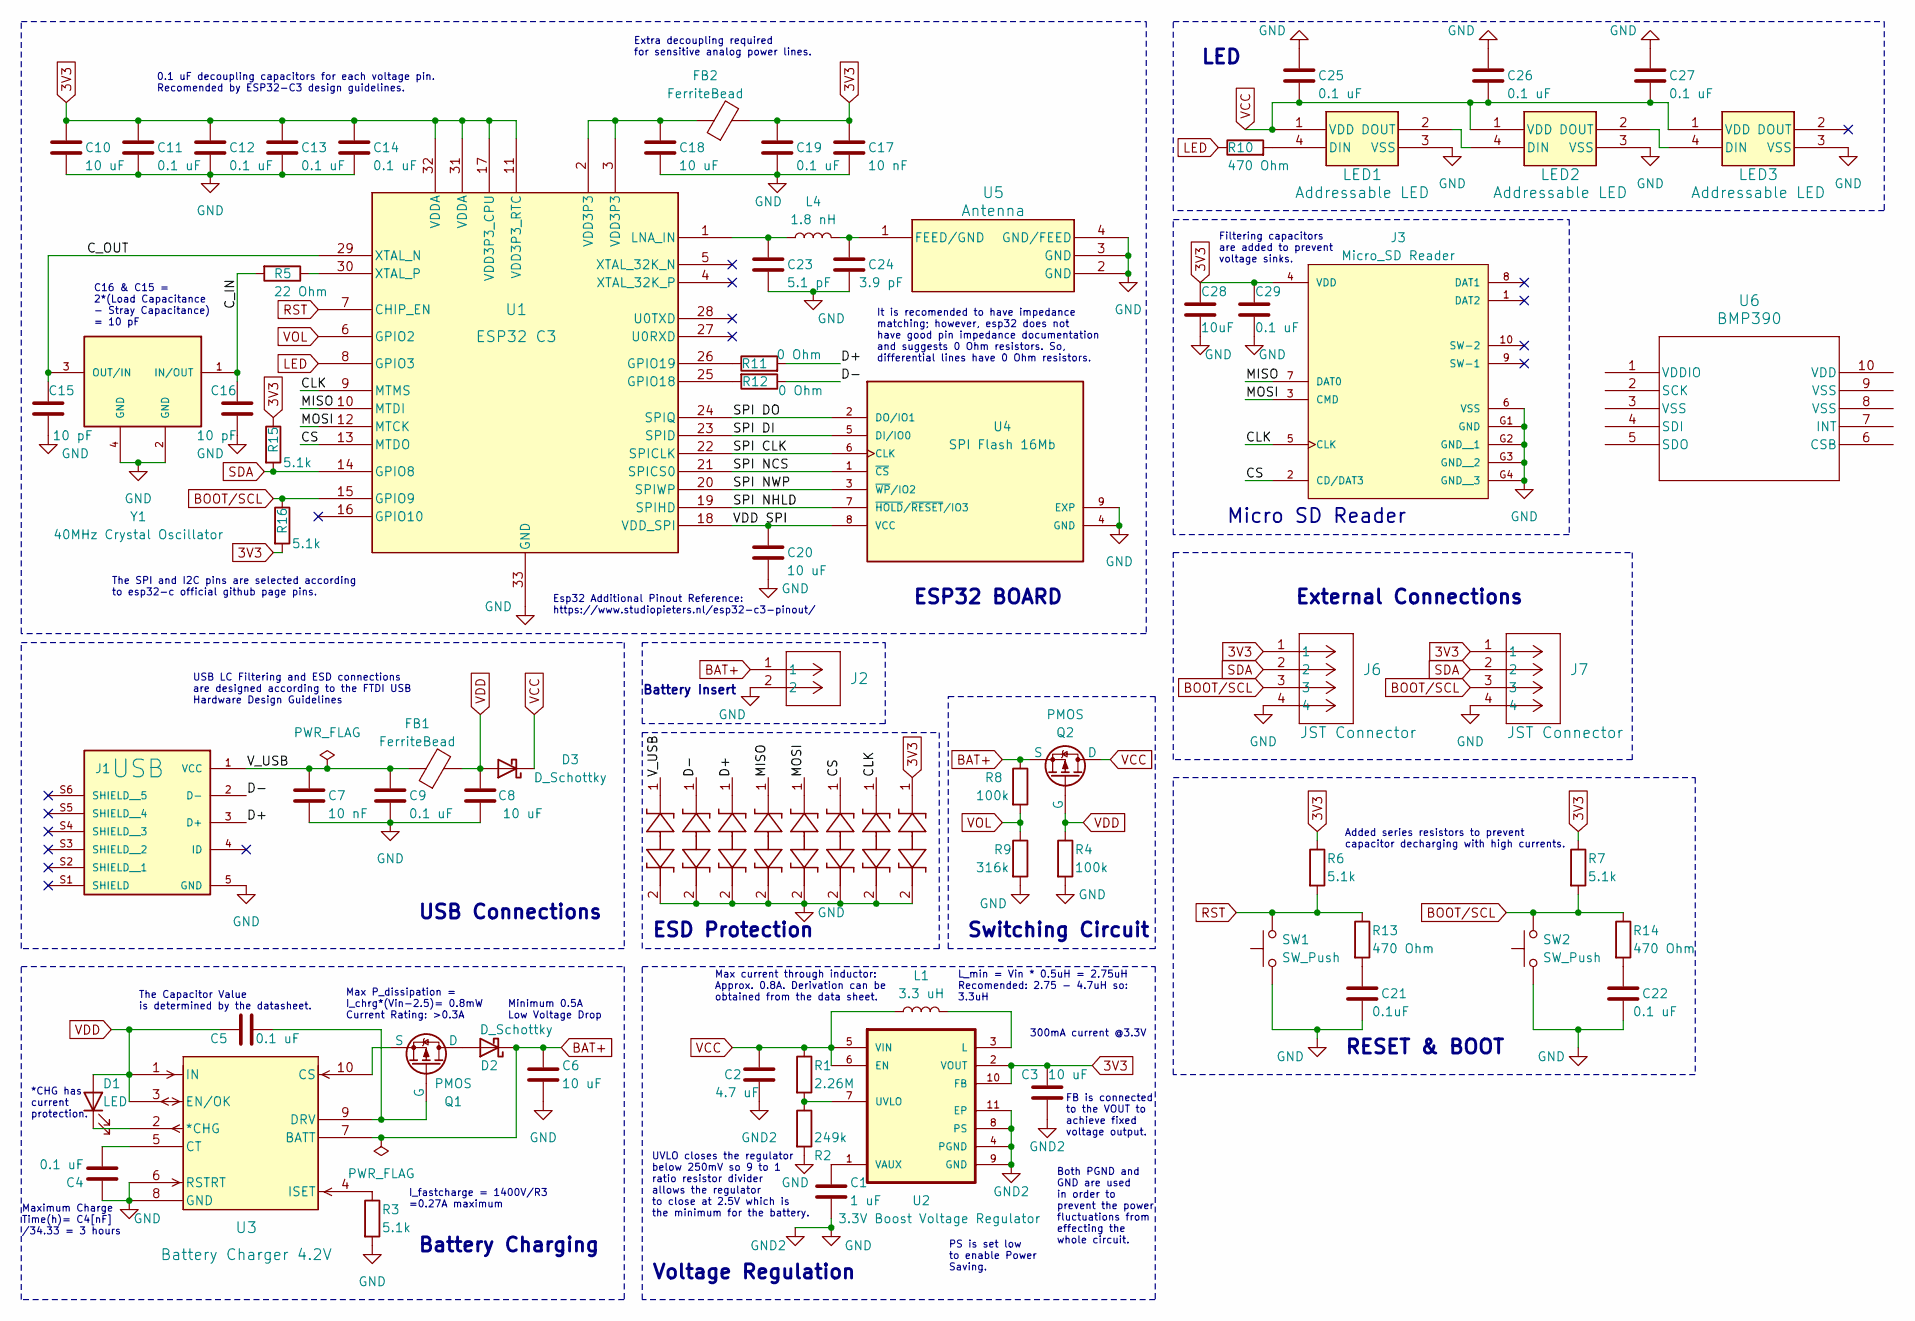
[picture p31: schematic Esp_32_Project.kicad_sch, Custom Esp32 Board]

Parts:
C1: 1 uF; C_0603_1608Metric_Pad1.08x0.95mm_HandSolder
C2: 4.7 uF; C_0603_1608Metric_Pad1.08x0.95mm_HandSolder
C3, C6, C8, C10, C18, C20: 10 uF; C_0603_1608Metric_Pad1.08x0.95mm_HandSolder
C4, C5, C9, C11, C12, C13, C14, C19, C22, C25, C26, C27, C29: 0.1 uF; C_0603_1608Metric_Pad1.08x0.95mm_HandSolder
C7, C17: 10 nF; C_0603_1608Metric_Pad1.08x0.95mm_HandSolder
C15, C16: 10 pF; C_0603_1608Metric_Pad1.08x0.95mm_HandSolder
C21: 0.1uF; C_0603_1608Metric_Pad1.08x0.95mm_HandSolder
C23: 5.1 pF; C_0603_1608Metric_Pad1.08x0.95mm_HandSolder
C24: 3.9 pF; C_0603_1608Metric_Pad1.08x0.95mm_HandSolder
C28: 10uF; C_0603_1608Metric_Pad1.08x0.95mm_HandSolder
CR1, CR2, CR3, CR4, CR5, CR6, CR7, CR8: ESD Protection; CR_SP3022_LTF
D1: LED; LED_0603_1608Metric_Pad1.05x0.95mm_HandSolder
D2, D3: D_Schottky; D_SMB_Handsoldering
FB1, FB2: FerriteBead; L_0201_0603Metric_Pad0.64x0.40mm_HandSolder
J1: USB; AMPHENOL_10118192-0002LF; PARTREV B
J2: Battery Connector; JST_XH_B2B-XH-A_1x02_P2.50mm_Vertical
J3: Micro_SD Reader; MicroSD Reader; PARTREV B2
J6, J7: JST Connector; JST_XH_B4B-XH-A_1x04_P2.50mm_Vertical
L1: 3.3 uH; L_0805_2012Metric_Pad1.05x1.20mm_HandSolder
L4: 1.8 nH; L_0402_1005Metric_Pad0.77x0.64mm_HandSolder
LED1, LED2, LED3: Addressable LED
Q1: PMOS; SOT-23-3
Q2: PMOS; SOT-323_SC-70_Handsoldering
R1: 2.26M; R_0603_1608Metric_Pad0.98x0.95mm_HandSolder
R2: 249k; R_0603_1608Metric_Pad0.98x0.95mm_HandSolder
R3, R6, R7, R15, R16: 5.1k; R_0603_1608Metric_Pad0.98x0.95mm_HandSolder
R4, R8: 100k; R_0603_1608Metric_Pad0.98x0.95mm_HandSolder
R5: 22 Ohm; R_0603_1608Metric_Pad0.98x0.95mm_HandSolder
R9: 316k; R_0603_1608Metric_Pad0.98x0.95mm_HandSolder
R10, R13, R14: 470 Ohm; R_0603_1608Metric_Pad0.98x0.95mm_HandSolder
R11, R12: 0 Ohm; R_0603_1608Metric_Pad0.98x0.95mm_HandSolder
SW1, SW2: SW_Push; Button
U1: ESP32 C3; QFN32_5X5_EXP
U2: 3.3V Boost Voltage Regulator; VREG_V62_16624-01YE
U3: Battery Charger 4.2V; 21-0061L_MXM
U4: SPI Flash 16Mb; IC_W25Q16JVUXIQ_TR; PARTREV H; DigiKey_Part_Number 256-W25Q16JVUXIQTR-ND
U5: Antenna; 2450AT18D0100E_JOT
U6: BMP390; LGA10_BMP390_BOS
Y1: 40MHz Crystal Oscillator; XTAL_ECS-400-9-36B-CKY-TR; DigiKey_Part_Number XC3060TR-ND

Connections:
3V3: C3.1, C10.1, C11.1, C12.1, C13.1, C14.1, C17.1, C19.1, C28.1, C29.1, CR8.1, FB2.2, J3.4 (VDD), J6.1, J7.1, R6.1, R7.1, R15.1, R16.2, U1.11 (VDD3P3_RTC), U1.17 (VDD3P3_CPU), U1.31 (VDDA), U1.32 (VDDA), U2.2 (VOUT), U2.10 (FB)
/CLK: CR7.1, J3.5 (CLK), U1.9 (MTMS)
/CS: CR6.1, J3.2 (CD/DAT3), U1.13 (MTDO)
/C_IN: C16.1, R5.2, Y1.1 (IN/OUT)
/C_OUT: C15.1, U1.29 (XTAL_N), Y1.3 (OUT/IN)
/D+: CR3.1, J1.3 (D+), R11.2
/D-: CR2.1, J1.2 (D-), R12.1
/MISO: CR4.1, J3.7 (DAT0), U1.10 (MTDI)
/MOSI: CR5.1, J3.3 (CMD), U1.12 (MTCK)
/SPI CLK: U1.22 (SPICLK), U4.6 (CLK)
/SPI DI: U1.23 (SPID), U4.5 (DI/IO0)
/SPI DO: U1.24 (SPIQ), U4.2 (DO/IO1)
/SPI NCS: U1.21 (SPICS0), U4.1 (~CS)
/SPI NHLD: U1.19 (SPIHD), U4.7 (~HOLD/~RESET/IO3)
/SPI NWP: U1.20 (SPIWP), U4.3 (~WP/IO2)
/VDD SPI: C20.1, U1.18 (VDD_SPI), U4.8 (VCC)
/V_USB: C7.1, C9.1, CR1.1, FB1.1, J1.1 (VCC)
BAT+: C6.1, D2.1 (K), J2.1, Q2.3 (S), R8.1, U3.7 (BATT)
BOOT/SCL: J6.3, J7.3, R7.2, R14.1, R16.1, SW2.2, U1.15 (GPIO9)
GND: C1.2, C2.2, C3.2, C4.1, C6.2, C7.2, C8.1, C9.2, C10.2, C11.2, C12.2, C13.2, C14.2, C15.2, C16.2, C17.2, C18.2, C19.2, C20.2, C21.2, C22.2, C23.2, C24.2, C25.1, C26.1, C27.1, C28.2, C29.2, CR1.2, CR2.2, CR3.2, CR4.2, CR5.2, CR6.2, CR7.2, CR8.2, J1.5 (GND), J2.2, J3.6 (VSS), J3.G1 (GND), J3.G2 (GND__1), J3.G3 (GND__2), J3.G4 (GND__3), J6.4, J7.4, LED1.3 (VSS), LED2.3 (VSS), LED3.3 (VSS), R2.2, R3.2, R4.2, R9.2, SW1.1, SW2.1, U1.33 (GND), U2.4 (PGND), U2.8 (PS), U2.9 (GND), U2.11 (EP), U3.6 (RSTRT), U3.8 (GND), U4.4 (GND), U4.9 (EXP), U5.2 (GND), U5.3 (GND), U5.4 (GND/FEED), Y1.2 (GND), Y1.4 (GND)
LED: R10.1, U1.8 (GPIO3)
unnamed: C18.1, FB2.1, U1.2 (VDD3P3), U1.3 (VDD3P3)
unnamed: C21.1, R13.2
unnamed: C22.1, R14.2
unnamed: D1.1 (K), U3.2 (*CHG)
unnamed: D2.2 (A), Q1.1 (D)
unnamed: LED1.4 (DIN), R10.2
unnamed: LED1.2 (DOUT), LED2.4 (DIN)
unnamed: LED2.2 (DOUT), LED3.4 (DIN)
unnamed: C5.2, Q1.2 (G), U3.9 (DRV)
unnamed: Q1.3 (S), U3.10 (CS)
unnamed: R12.2, U1.25 (GPIO18)
unnamed: R11.1, U1.26 (GPIO19)
unnamed: C23.1, L4.1, U1.1 (LNA_IN)
unnamed: R5.1, U1.30 (XTAL_P)
unnamed: L1.2, U2.3 (L)
unnamed: R1.2, R2.1, U2.7 (UVLO)
unnamed: C1.1, U2.1 (VAUX)
unnamed: C4.2, U3.5 (CT)
unnamed: R3.1, U3.4 (ISET)
unnamed: C24.1, L4.2, U5.1 (FEED/GND)
RST: R6.2, R13.1, SW1.2, U1.7 (CHIP_EN)
SDA: J6.2, J7.2, R15.2, U1.14 (GPIO8)
VCC: C2.1, C25.2, C26.2, C27.2, D3.1 (K), L1.1, LED1.1 (VDD), LED2.1 (VDD), LED3.1 (VDD), Q2.1 (D), R1.1, U2.5 (VIN), U2.6 (EN)
VDD: C5.1, C8.2, D1.2 (A), D3.2 (A), FB1.2, Q2.2 (G), R4.1, U3.1 (IN), U3.3 (EN/OK)
VOL: R8.2, R9.1, U1.6 (GPIO2)

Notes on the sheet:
USB LC Filtering and ESD connections are designed according to the FTDI USB Hardware Design Guidelines
Battery Charging
FB is connected to the VOUT to achieve fixed voltage output.
Voltage Regulation
ESP32 BOARD
ESD Protection
Extra decoupling required for sensitive analog power lines.
Max P_dissipation = I_chrg*(Vin-2.5)= 0.8mW Current Rating: >0.3A
The SPI and I2C pins are selected according to esp32-c official github page pins.
Minimum 0.5A Low Voltage Drop
The Capacitor Value is determined by the datasheet.
L_min = Vin * 0.5uH = 2.75uH Recomended: 2.75 - 4.7uH so: 3.3uH
300mA current @3.3V
UVLO closes the regulator below 250mV so 9 to 1 ratio resistor divider allows the regulator to close at 2.5V which is the minimum for the battery.
Filtering capacitors are added to prevent voltage sinks.
Micro SD Reader
I_fastcharge = 1400V/R3 =0.27A maximum
Esp32 Additional Pinout Reference: https://www.studiopieters.nl/esp32-c3-pinout/
LED
It is recomended to have impedance matching; however, esp32 does not have good pin impedance documentation and suggests 0 Ohm resistors. So, differential lines have 0 Ohm resistors.
Both PGND and GND are used in order to prevent the power fluctuations from effecting the whole circuit.
RESET & BOOT
*CHG has current protection.
PS is set low to enable Power Saving.
External Connections
Max current through inductor: Approx. 0.8A. Derivation can be obtained from the data sheet.
Battery Insert
0.1 uF decoupling capacitors for each voltage pin. Recomended by ESP32-C3 design guidelines.
USB Connections
C16 & C15 = 2*(Load Capacitance - Stray Capacitance) = 10 pF
Maximum Charge Time(h)= C4[nF] /34.33 = 3 hours
Switching Circuit
Added series resistors to prevent capacitor decharging with high currents.

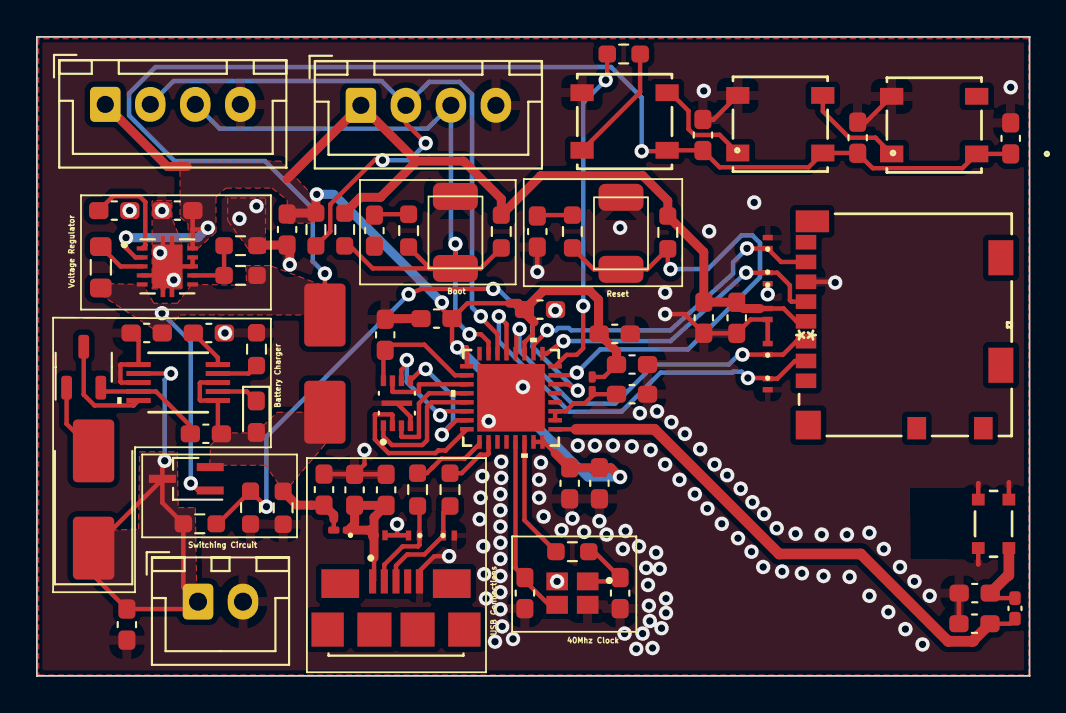
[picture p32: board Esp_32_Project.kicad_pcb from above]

Board: 2 copper layers, 55.1 x 35.5 mm, 78 parts (0 on the bottom side), 46 nets.

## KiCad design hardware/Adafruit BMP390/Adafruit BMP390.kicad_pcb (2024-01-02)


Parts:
C4, C5: 10uF; 0805-NO
C6: 0.1uF; 0603-NO
CONN3, CONN4: STEMMA_I2C_QT; JST_SH4
D1: GREEN; CHIPLED_0603_NOOUTLINE
D2: 1N4148; SOD-323
FID3, FID4: FIDUCIAL_1MM
IC1: BMP388
JP1: HEADER-1X870MIL; 1X08_ROUND_70
Q2: BSS138; SOT363
R1, R4, R5: 10K; 0603-NO
R2: 10K; RESPACK_4X0603
SJ1: SOLDERJUMPER; SOLDERJUMPER_ARROW_NOPASTE
U1: AP2112K-3.3; SOT23-5
U$40, U$41: MOUNTINGHOLE2.5; MOUNTINGHOLE_2.5_PLATED

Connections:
3.3V: C5.1, C6.1, IC1.1 (VDDIO), IC1.10 (VDD), JP1.2, Q2.2 (G), Q2.5 (G), R1.2, R2.2 (1), R2.4 (1), R4.2, R5.1, U1.5 (OUT)
CS: D2.C, JP1.7
CS_3V: D2.A, IC1.6 (CSB), R1.1
GND: C4.2, C5.2, C6.2, CONN3.1 (GND), CONN3.MT1 (MT), CONN3.MT2 (MT), CONN4.1 (GND), CONN4.MT1 (MT), CONN4.MT2 (MT), D1.C, IC1.3 (GND), IC1.8 (GND), IC1.9 (GND), JP1.3, SJ1.2, U1.2 (GND)
INT: IC1.7 (INT), JP1.8
unnamed: D1.A, R5.2
SCK/SCL: CONN3.4 (SCL), CONN4.4 (SCL), JP1.4, Q2.6 (D), R2.8 (2)
SCK_3V: IC1.2 (SCK), Q2.1 (S), R2.7 (2)
SDI/SDA: CONN3.3 (SDA), CONN4.3 (SDA), JP1.6, Q2.3 (D), R2.6 (2)
SDI_3V: IC1.4 (SDI), Q2.4 (S), R2.5 (2)
SDO/ADR: IC1.5 (SDO), JP1.5, R4.1, SJ1.1
VCC: C4.1, CONN3.2 (V+), CONN4.2 (V+), JP1.1, R2.1, R2.3 (1), U1.1 (IN), U1.3 (EN)

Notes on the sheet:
For SPI set CSB low at startup SDO=MISO, SDI=MOSI, SCK=SCK, CSB=CS/SSEL
ON LED
LEVEL SHIFTING (5V <--> 3V)
I2C Pullups & Shift
For I2C leave CSB pulled high (default value) SDI=SDA, SCK=SCL
STEMMA/I2C Headers
Power supply



Board: 2 copper layers, 25 parts (5 on the bottom side), 12 nets.

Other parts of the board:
U$2: ADAFRUIT_2.5MM
U$46: ADAFRUIT_3.5MM
U$47: PCBFEAT-REV-040
U$48, U$49: STEMMAQT

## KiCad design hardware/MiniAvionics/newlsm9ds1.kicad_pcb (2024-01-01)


Board: 2 copper layers, 13.8 x 19.4 mm, 17 parts (0 on the bottom side), 13 nets.

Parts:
C1: 0.22uF; C_0603_1608Metric_Pad1.08x0.95mm_HandSolder
C2: 0.01uF; C_0603_1608Metric_Pad1.08x0.95mm_HandSolder
C3: 100nF; C_0603_1608Metric_Pad1.08x0.95mm_HandSolder
C4: 10uf; C_0603_1608Metric_Pad1.08x0.95mm_HandSolder
C6: 100uF; C_0603_1608Metric_Pad1.08x0.95mm_HandSolder
D1, D2: Diode; 1N4148W
D3: LED; LED_0603_1608Metric_Pad1.05x0.95mm_HandSolder
IC1: LSM9DS1; lsm9ds1TR
J1: 826629-4; CON4_1X4_P100UM_HDR2_TYC
R1, R2, R4, R5, R6, R7: 10k; R_0603_1608Metric_Pad0.98x0.95mm_HandSolder
R3: 10K; R_0603_1608Metric_Pad0.98x0.95mm_HandSolder

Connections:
3.3V: C3.1, C4.1, C6.1, IC1.1 (VDDIO), IC1.3 (VDDIO), IC1.22 (VDD), IC1.23 (VDD), J1.1, R1.1, R2.1, R3.1, R4.1, R5.1, R6.1, R7.1
/CS_A/G: D2.1 (A), IC1.7 (CS_A/G)
/CS_M: D1.1 (A), IC1.8 (CS_M)
/GND: C1.2, C2.2, C3.2, C4.2, C6.2, D3.1 (K), IC1.14 (RESERVED(GND)), IC1.15 (RESERVED(GND)), IC1.16 (RESERVED(GND)), IC1.17 (RESERVED(GND)), IC1.18 (RESERVED(GND)), IC1.19 (GND), IC1.20 (GND), J1.2
/SDO_AG: IC1.5 (SDO_A/G), R1.2
/SDO_M: IC1.6 (SDO_M), R7.2
unnamed: D1.2 (C), R4.2
unnamed: D2.2 (C), R5.2
unnamed: D3.2 (A), R3.2
unnamed: C1.1, IC1.24 (C1)
unnamed: C2.1, IC1.21 (CAP)
SDA: IC1.2 (SCL/SPC), R6.2
SDO: IC1.4 (SDA/SDI/SDO), R2.2

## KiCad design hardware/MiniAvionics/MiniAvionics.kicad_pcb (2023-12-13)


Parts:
C1, C2: 0.1uF; R_0603_1608Metric
GREEN1: LED; R_0603_1608Metric
J1: 826629-4; CON4_1X4_P100UM_HDR2_TYC
R1, R2: 4.7k; R_0603_1608Metric
R3: 10k; R_0603_1608Metric
U1: BMP390; LGA10_BMP390_BOS-L

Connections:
/BMP390/I2C_PS: J1.2, U1.5 (SDO)
/BMP390/INT: U1.7 (INT)
/BMP390/SCL: R1.1, U1.2 (SCK)
/BMP390/SDA: J1.3, R2.1, U1.4 (SDI)
GND: C1.2, C2.2, GREEN1.1 (K), J1.4, U1.3 (VSS), U1.8 (VSS), U1.9 (VSS)
unnamed: GREEN1.2 (A), R3.2
VDD: C1.1, C2.1, J1.1, R1.2, R2.2, R3.1, U1.1 (VDDIO), U1.6 (CSB), U1.10 (VDD)


Board: 2 copper layers, 12.9 x 11.1 mm, 8 parts (0 on the bottom side), 6 nets.

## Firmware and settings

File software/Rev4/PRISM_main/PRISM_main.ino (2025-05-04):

#include "data_class.h"
#include "imu_class.h"
#include "altimeter_class.h"
#include "kalman_class.h"
#include "led_class.h"
#include "gps_class.h"
#include "radio_class.h"
#include "stepper_class.h"

#include <Arduino.h>


// pinmodes
#define KEYSWITCH A8
// PYRO 1 (top) = PIN 24
// PYRO 2 (bottom) = PIN 25
#define BUZZER 6
#define MAIN 24
#define DROGUE 25


byte IICdata[5] = {0, 0, 0, 0, 0}; // buffer for sensor data
bool debugEnable=false; //Enable debug printing
bool noSD = false;  // Enable debug without sd
short int flight_phase = 1;
unsigned long loop_t_start = 0;
unsigned long loop_t_end = 0;
float minimumAltitude;
float minimumDROGUEAltitude;
float minimumMainAltitude = 152; // 152 [meters] set on launch day (main deploy)
float trigger_offset = 30; // 30 [meters] set on launch day  (launch detect)
float DROGUE_velocity_trigger = -3; //-3[m/s] set on launch day (apogee detect)

float pyro_t_start = 0; //start time of pyro event
float beep_t_start = 0;
bool beep=false;


// setup sensors
Led statusLed1(0);
Data data(&statusLed1);
Imu imu(&data);
Kalman kalman_filter(&data);
Altimeter altimeter(&data);

//EAST
Radio radio(&data);
Gps gps(&radio);

StepperMotor steppermotor;

unsigned long cycle_time;
unsigned long old_cycle_time = 0;

void setup()
{
<<<<<<< HEAD
  steppermotor.enable_stepper();
//  steppermotor.home_stepper();
  Serial.begin(115200);
  tone(BUZZER,1500,1000);
  radio.led_test(&statusLed1);
  delay(10);
=======
    steppermotor.enable_stepper();
    steppermotor.home_stepper();
    Serial.begin(115200);
    tone(BUZZER,1500,1000);
    radio.led_test(&statusLed1);
    delay(10);
>>>>>>> d2b5f4d48bb77750b1b70c9f78fa249325ea778c

    Serial.print(CrashReport);
    delay(1000);
    
    radio.begin();
    gps.begin_gps(&statusLed1);
    
    pinMode(DROGUE,OUTPUT);
    pinMode(MAIN,OUTPUT);
    digitalWrite(DROGUE, LOW);  //very important!!
    digitalWrite(MAIN, LOW);  //very important!!
    while(analogRead(KEYSWITCH) >= 100) {
        tone(BUZZER, 700, 100);
        delay(200);
    };
  
    Serial.println("To enter debug mode, send any character over Serial; proceeding without debug mode in:");
    delay(5000);
    int countdown=10;
    while(Serial.available()==0) {
        Serial.println(countdown--);
        delay(200);
        if(millis()>10000) {
            break;
        }
    }
    if(Serial.available()!=0) {
        debugEnable=true;
        Serial.println("Entered debug mode");
        noSD = true;
        Serial.println("Entered no SD mode");  
        debugflight_phase();
    }
    else
    {
        Serial.println("Debug mode not enabled; proceeding normally");
    }

    // begin sensors
    data.SDbegin(debugEnable, noSD);
    imu.begin_imu(debugEnable);
    altimeter.begin_altimeter(debugEnable);
    data.kfx(DROGUE_velocity_trigger);
}

void loop()
{
    loop_t_start = micros();
    //EAST
    cycle_time = millis() - old_cycle_time;
    
    if(cycle_time > 1000){
        gps.read_position();
        old_cycle_time = millis();
    }
  
    // radio
    radio.sendRadio();

    steppermotor.move_stepper(1);

<<<<<<< HEAD
  //steppermotor.move_stepper(1);
  
=======
    // Chooses loop to run through depending on what the flight_phase is set to
    switch (flight_phase)
    {
>>>>>>> d2b5f4d48bb77750b1b70c9f78fa249325ea778c

        // Prelaunch flight_phase 1: Before keyswitch
        case 1:
            PreARM();
            break;
      
        // Prelaunch flight_phase 2: After keyswitch
        case 2:
            PostARM();
            break;
      
        // Lauched but before apogee
        case 3:
            BeforeApogee();
            break;
      
        // After apogee before main deploy
        case 4:
            BeforeMain();
            break;
        
          // After main deploy
        case 5:
            AfterMain();
            break;
        
    }
    
    loop_t_end = micros();
    // adjust delay based on length of loop
    if((loop_t_end - loop_t_start) < 10000){
        delayMicroseconds(10000 - (loop_t_end - loop_t_start));
    }  
}


// launch flight_phase functions
// flight_phase 1
void PreARM()
{
    collect_data();

    // when keyswitch is turned, enter PostARM flight_phase
    if (analogRead(KEYSWITCH) >= 100) {
        tone(BUZZER, 400, 1000);
        kalman_filter.begin();
        float average_altitude = 0;
        int number_readings = 5;

        for (int freq = 400; freq <= 1000; freq += 100) {
            tone(BUZZER, freq, 100);
            delay(100);

            //take 5 reading and compute the averadge, then use this to set the launch detection altitude
            for (int i = 0; i < number_readings; i++){
                average_altitude += data.baralt();
                altimeter.perform_reading();
            }

            minimumAltitude = (average_altitude / number_readings) + trigger_offset;
            data.kfy(minimumAltitude);
            flight_phase = 2;
            debugflight_phase();
        }
        tone(BUZZER, 200, 3000);
    }
}

// flight_phase 2
void PostARM()
{
    collect_data();
    kalman_filter.update();
    statusLed1.RGB2(0, 255, 255, 0); // Yellow for LED 1
    //statusLed2.RGB2(1, 255, 255, 0); // Yellow for LED 2

    if (data.baralt() > minimumAltitude) {
        // launch
        flight_phase = 3;
        debugflight_phase();
    }
    if (analogRead(KEYSWITCH) <= 100) {
        // turned off
        flight_phase = 1;
        debugflight_phase();
    }
}

// flight_phase 3
void BeforeApogee()
{ 
    collect_data();
    status_lights();
    kalman_filter.update();

<<<<<<< HEAD
  //if below apogee velocity threshold, power the drogue pyro
  if (data.kfvz() < DROGUE_velocity_trigger) {
    // deploy drogue
    pyro_t_start = data.curtime();
 //   digitalWrite(DROGUE, HIGH);
//    tone(33, 1000);
    flight_phase = 4; 
    debugflight_phase(); 
    Serial.println("Drouge Deploy");
  }
=======
    //if below apogee velocity threshold, power the drogue pyro
    if (data.kfvz() < DROGUE_velocity_trigger) {
        // deploy drogue
        pyro_t_start = data.curtime();
        digitalWrite(DROGUE, HIGH);
        // tone(33, 1000);
        flight_phase = 4; 
        debugflight_phase();
    }
>>>>>>> d2b5f4d48bb77750b1b70c9f78fa249325ea778c
}

// flight_phase 4
void BeforeMain()
{ 
    collect_data();
    status_lights();
    kalman_filter.update();

    //if pyro has been on for 1s, turn it off
    if (data.curtime() > (pyro_t_start + 1000)){
        digitalWrite(DROGUE, LOW);
        noTone(33);
    }

<<<<<<< HEAD
  //if at main deploy, power the main pyro
  if ((data.curtime() > (pyro_t_start + 5000)) & (data.baralt() < (minimumMainAltitude + minimumAltitude))){
    // deploy main parachute
    pyro_t_start = data.curtime();
    //digitalWrite(MAIN, HIGH);
//    tone(33, 500);
    flight_phase = 5;
    debugflight_phase();
    Serial.println("Main Deploy");
  }
=======
    //if at main deploy, power the main pyro
    if ((data.curtime() > (pyro_t_start + 5000)) & (data.baralt() < (minimumMainAltitude + minimumAltitude))) {
        // deploy main parachute
        pyro_t_start = data.curtime();
        digitalWrite(MAIN, HIGH);
        // tone(33, 500);
        flight_phase = 5;
        debugflight_phase();
    }
>>>>>>> d2b5f4d48bb77750b1b70c9f78fa249325ea778c
}

// flight_phase 5
void AfterMain(){
    collect_data();
    statusLed1.RGB2(0, 0, 255, 0); // Green for LED 1
    // statusLed2.RGB2(1, 0, 255, 0); // Green for LED 2

    kalman_filter.update();

    //if pyro has been on for 1s, turn it off
    if (!beep & (data.curtime() > (pyro_t_start + 1000))) {
        digitalWrite(MAIN, LOW);
        noTone(33);
        beep=true;
    }
    if (beep & (data.curtime() > (beep_t_start + 4000))) {
        tone(33, 2000, 500);
        beep_t_start=data.curtime();
    }
  //loop?
  // First burst
//    tone(BUZZER, 1500, 1000); // 1.5 kHz tone for 1 second
//    delay(1000); // Wait for 1 second
//
//  // Second burst
//  tone(BUZZER, 1500, 1000); // 1.5 kHz tone for 1 second
//  delay(7000); // Wait for 7 seconds
}


// helper functions

// collect data function
void collect_data (void){
    // contains all sensor callings
    imu.read_and_fuse();
    altimeter.perform_reading();
    data.curtime((float)millis());
    data.readGPS();
    data.phs(flight_phase);
    data.analogTelem();
    data.encodeAndAdd();
    data.diagmsg_reset(); // clear out previous diagnostic messages
}

// neopixels
void status_lights (void) {
    statusLed1.RGB2(0, 100, 0, 0);
}

void debugflight_phase()
{
<<<<<<< HEAD
  if(debugEnable==false)
  {
    Serial.print("flight_phase ");
    Serial.println(flight_phase);
  }
=======
    if(debugEnable==true) {
        Serial.print("flight_phase ");
        Serial.println(flight_phase);
    }
>>>>>>> d2b5f4d48bb77750b1b70c9f78fa249325ea778c
}

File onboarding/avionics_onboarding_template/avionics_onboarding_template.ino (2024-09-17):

#include <iostream>
#include <string>
using namespace std;
#include <SPI.h>

#define HSPI_MISO   12
#define HSPI_MOSI   13
#define HSPI_SCLK   14
#define HSPI_SS     16
#define OE          21

uint8_t numbercodes[11] = {
    // Reversed bits for each original byte
    0b11101011, // 0
    0b00101000, // 1
    0b10110011, // 2
    0b10111010, // 3
    0b01111000, // 4
    0b11011010, // 5
    0b11011011, // 6
    0b10101000, // 7
    0b11111011, // 8
    0b11111010, // 9
    0b00000100  // .
};

char digits1[32];
char digits2[32];
uint32_t stream = 0;
float counter=0;
std::string digit;
std::string nextdigit;
long timing = millis();
int brightness = 100;
int char1;
int char2;
int numeral;
int iter = 0;

//uninitalised pointers to SPI objects
SPIClass * hspi = NULL;
static const int spiClk = 1000000; // 1 MHz

void setup() {
  //initialise two instances of the SPIClass attached to VSPI and HSPI respectively
  hspi = new SPIClass(HSPI);
 
  hspi->begin(HSPI_SCLK, HSPI_MISO, HSPI_MOSI, HSPI_SS); //SCLK, MISO, MOSI, SS
  
  //set up slave select pins as outputs as the Arduino API
  //doesn't handle automatically pulling SS low
  pinMode(hspi->pinSS(), OUTPUT); //HSPI SS
  pinMode(OE, OUTPUT);SC
  Serial.begin(115200);
  radio.begin();
  Serial.println("Booted");
}

void loop() {
  radio.receivePacket();
  disp(analogRead(33)*0.00105006, 1000, iter);
  iter++;
  if(iter>=5)
  {
    iter=0;
  }
}

void disp(float number1, float number2, int addr)
{
  
}

void spiCommand(SPIClass *spi, uint32_t bits) {
  //use it as you would the regular arduino SPI API
  spi->beginTransaction(SPISettings(spiClk, MSBFIRST, SPI_MODE0));
  digitalWrite(spi->pinSS(), HIGH); //pull SS slow to prep other end for transfer
  spi->transfer32(bits);
  digitalWrite(spi->pinSS(), LOW); //pull ss high to signify end of data transfer
  spi->endTransaction();
}

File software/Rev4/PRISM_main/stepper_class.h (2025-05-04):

#include <Arduino.h>
#include <SpeedyStepper.h>
#include <TMCStepper.h>
#define DRIVER_ADDRESS 0b00 // TMC2209 Driver address according to MS1 and MS2
#define SERIAL_PORT Serial4
#define R_SENSE 0.11f // Match to your driver
class StepperMotor
{

private:
  //pin definitions
  const uint8_t step_pin = 15;
  const uint8_t dir_pin = 20;
  const uint8_t tx_pin = 17;
  const uint8_t rx_pin = 16;

  TMC2209Stepper driver;
  SpeedyStepper stepper;
  int home_speed = 180; //deg/s
  int micro_steps_per_step = 4;
  int full_steps_per_rot = 200;

  const uint8_t run_current_percent = 50;
  const uint8_t stall_guard_threshold = 120;
  int max_speed = 85000; //deg/s
  int max_accel = 2000; //deg/s/s



  //TMC2209 driver object
  //Step Contoller object
  

public:
  StepperMotor();
  void init();
  void enable_stepper();
  void home_stepper();
  void move_stepper(int pos);
  void disable_stepper();
  
};

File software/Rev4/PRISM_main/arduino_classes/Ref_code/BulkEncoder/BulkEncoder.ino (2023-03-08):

union floatunion_t {
    float f;
    char a[sizeof (float) ];
} float_u;

void bulkencode(char* in, char* out) {
  //in and out should be char arrays of the same size
  for (int i=0; i<sizeof(in)/sizeof(in[0]); i++)
  {
    char encoded[sizeof (float) ];
    encoder(encoded, in[i]);
    encoder(encoded, in[i]);
    for(int j=0; j<sizeof(float); j++)
    {
      out[i*sizeof(float)+j]=encoded[j];
    }
  }
//  Serial.println("Encoded");
//  Serial.print(String(sizeof(packet)/sizeof(packet[0]))+": ");
//  for (int k=0; k<sizeof(packet)/sizeof(packet[0]); k++)
//  {
//    Serial.print(packet[k]);
//  }
}

void encoder(char* encoded, float input)
{
  float_u.f=input;
  for (int i = 0; i<sizeof (float); i++)
  {
    encoded[i] = float_u.a[i];
  }
}

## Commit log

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2022-11-11 Update Avoinics Power System.kicad_sch
    [Avoinics Power System.kicad_sch]
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2022-11-29 Add edited board 4 and main prism teensy schematics
    [board_4.kicad_pcb, board_4.kicad_sch, board_one_teensy_22.kicad_pcb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]
2022-11-30 Add voltage divider for measuring battery
    [board_one_teensy_22.kicad_sch]
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2022-12-06 Add buzzer and take out 2nd SPI
    [board_4.kicad_sch, board_one_teensy_22.kicad_sch]
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2022-12-07 add footprint for IO connector
    [CoreIO.kicad_sch]
2022-12-08 changed resistor values on IO
    [CoreIO.kicad_sch]
2022-12-09 Add footprints to resistors and LEDs
    [board_4.kicad_sch]
2023-02-06 add new arm switches
    [CoreIO.kicad_pcb, CoreIO.kicad_sch, D2F-01F.step]
2023-02-11 Reverse Current
    [CoreIO.kicad_pcb, CoreIO.kicad_sch, REV2_SPRING_2022.kicad_sch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]
2023-02-15 Added EAST outline versions
    [EAST_PCB_outline.dxf, EAST_PCB_outline_with_headers.dxf]
2023-02-15 Fixed extraneous lines in EAST outline
    [EAST_PCB_outline_with_headers.dxf]
2023-02-22 Revise PCB outlines with SD clip and new headers.
    [EAST_PCB_outline.dxf, EAST_PCB_outline_with_2x10_headers_and_sd_clip.dxf, EAST_PCB_outline_with_3x7_headers.dxf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]
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2023-02-22 Add GPS symbol and EAST PCB outline.
    [EAST_PCB_no_sd_clip.dxf]
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2023-02-22 Add GPS project to facilitate future reference.
    [Qwiic GPS - Titan X1 v10.kicad_pcb, Qwiic GPS - Titan X1 v10.kicad_sch]
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2023-02-23 work on PRISM io
    [CoreIO.kicad_pcb, CoreIO.kicad_sch, PRISM_IO_PCB.dxf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]
2023-02-24 Update east gps layout
    [EAST_GPS.kicad_pcb]
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2023-02-25 Add altimeter to footprint
    [board_one_teensy_22.kicad_pcb]
2023-02-25 Edit footprint layout and resistor sizes
    [board_one_teensy_22.kicad_pcb, board_one_teensy_22.kicad_sch]
2023-02-25 Add east teensy footprint
    [EAST_GPS.kicad_pcb, EAST_GPS.kicad_sch, board_4.kicad_pcb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]
2023-02-25 Change teensy serial labeling
    [board_4.kicad_sch]
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2023-02-26 Update east communication and layout
    [EAST_GPS.kicad_pcb, EAST_GPS.kicad_sch]
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2023-02-26 fixed some footprints on PRISM IO
    [CoreIO.kicad_pcb, CoreIO.kicad_sch, CoreIO.step]
2023-02-26 Add connector layout to PCB DXFs
    [EAST_PCB_outline_with_2x8_headers.dxf, PRISM_IO_PCB_with_connectors.dxf, PRISM_MAIN_PCB_with_sd_clip_and_connectors.dxf]
2023-02-27 add footprint for diode
    [CoreIO.kicad_pcb, CoreIO.kicad_sch]
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2023-02-28 Complete PRISM Teensy layout
    [CoreIO.kicad_sch, board_4.kicad_pcb, board_one_teensy_22.kicad_pcb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]
2023-02-28 Switch connector pin order on IO
    [CoreIO.kicad_sch, EAST_GPS.kicad_pcb, EAST_GPS.kicad_sch]
2023-02-28 Relocate USB-micro on main Teensy
    [board_one_teensy_22.kicad_pcb]
2023-02-28 Completed EAST Teensy board, confused at GPS board
    [EAST_GPS.kicad_pcb, EAST_GPS.kicad_sch, board_4.kicad_pcb]
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2023-03-01 Edit layout of board 4
    [board_4.kicad_pcb]
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2023-03-03 Rough layout of main teensy board
    [board_one_teensy_22.kicad_pcb, board_one_teensy_22.kicad_sch]
2023-03-04 Add rough layout arrangement
    [board_one_teensy_22.kicad_pcb]
2023-03-04 Final PRISM Teensy Layout
    [PRISM_MAIN_PCB_final.dxf]
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2023-03-04 update core IO with minor changes
    [CoreIO.kicad_pcb, SM02B-SFHRS-TF.STEP]
2023-03-04 new dxf for prism io
    [CoreIO.kicad_pcb, PRISM_IO_PCB_with_connectors.dxf]
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2023-03-05 Fix errors on TX/RX and added buzzer
    Current state: Board 1 - need to check diodes; Board 4 - done; GPS- not showing layout traces, all need logos
    [board_4.kicad_pcb, board_4.kicad_sch, board_one_teensy_22.kicad_pcb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]
2023-03-05 Add schottcky diodes to main teensy
    [board_one_teensy_22.kicad_pcb, board_one_teensy_22.kicad_sch]
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2023-03-06 finished CORE IO layout
    [CoreIO.kicad_pcb]
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2023-03-06 add mounting holes and update resistor size
    [CoreIO.kicad_pcb, CoreIO.kicad_sch]
2023-03-07 add plated holes to both east boards
    [EAST_GPS.kicad_pcb, board_4.kicad_pcb]
2023-03-07 Completed IO layout, added board 1 plated holes
    [CoreIO.kicad_pcb, board_one_teensy_22.kicad_pcb]
2023-03-07 Board one changed resistor size
    [board_one_teensy_22.kicad_pcb, board_one_teensy_22.kicad_sch]
2023-03-07 change board 4 C size and GPS labels hided
    [EAST_GPS.kicad_pcb, board_4.kicad_pcb, board_4.kicad_sch]
2023-03-07 minor fixes
    [CoreIO.kicad_pcb, EAST_GPS.kicad_pcb, board_4.kicad_pcb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]
2023-03-08 fixed 90deg trace
    [CoreIO.kicad_pcb]
2023-03-08 test gerber and bom generation
    [CoreIO-B_Cu.gbr, CoreIO-B_Mask.gbr, CoreIO-B_Paste.gbr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]
2023-03-08 Edit for design rule check
    [board_4.kicad_pcb]
2023-03-08 Fix CoreIO board
    [CoreIO.kicad_pcb]
2023-03-08 add square silk screen for GPS
    [EAST_GPS.kicad_pcb]
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2023-03-08 fix DRC errors on PRISM FC
    [board_one_teensy_22.kicad_pcb]
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2023-03-29 re structure the file system
    [4_15_22_test2.csv, 4_15_22_test3.csv, 4_15_22_test4.csv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]
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2023-03-29 Fix IMUf file structure
    [IMU.ino]
2023-03-31 Add mask layer for altimeter pads
    [board_one_teensy_22.kicad_pcb]
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2023-04-01 pcb fixes
    [EAST_GPS.kicad_pcb, EAST_GPS.kicad_sch, board_4.kicad_pcb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]
2023-04-02 fixed a few pcb silkscreen things
    [EAST_GPS.kicad_pcb, EAST_GPS.kicad_sch, board_4.kicad_pcb]
2023-04-02 Fixed decode, no more corruption
    [SDDecode.ino]
2023-04-02 Fix Radio testing code compile errors.
    [radio_class.ino]
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2023-04-02 Fix Radio sending buffer size.
    [radio_class.ino]
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2023-04-07 Fix integration of imu and data in main
    [PRISM_main.ino, imu_class.cpp]
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2023-04-07 Fix Data class order, remove ino
    [data_class.cpp]
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2023-04-12 removed LED stuff (will fix later)
    [PRISM_main.ino]
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2023-04-17 tried to integrate GPS
    Adding GPS prevents the serial transfer from working at full speed.
    [PRISM_main.ino, data_class.cpp, gps_class.cpp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]
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2023-04-19 fixed gps integration and changed gps status color
    [gps_class.cpp, radio_class.cpp]
2023-04-19 first kalman fix attempt
    [PRISM_main.ino, kalman_class.cpp]
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2023-10-09 Diagmsg error codes into gps
    [gps_class.cpp]
2023-10-21 Fix gps error code exponent
    [gps_class.cpp]
2023-10-25 Fix diagmsg inital value
    [data_class.cpp]
2023-10-25 added reset for diag message to fix GPS bug
    [PRISM_main.ino, data_class.cpp]
2023-10-26 replaced pyro trigger with no delay implementation - NEED TO TEST!!!!
    [PRISM_main.ino, data_class.cpp]
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2023-11-29 new buzzer replaced
    [board_one_teensy_22.kicad_sch]
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2023-12-06 Add log files and thrust test stand cals
    [0N.csv, 0N_Final.csv, 1075N.csv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]
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2023-12-06 created new symbol and footprint for buzzer
    [board_one_teensy_22.kicad_sch]
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2023-12-13 fixing merge conflict
    [0N.csv, 0N_Final.csv, 1075N.csv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]
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2024-01-02 Fix some issues with PRISM FC schematic
    [board_one_teensy_22.kicad_sch]
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2024-01-02 Fix file name issue
    [board_one_teensy_22.kicad_pcb, board_one_teensy_22.kicad_sch]
2024-01-02 Need to fix SD slot still
    [board_one_teensy_22.kicad_pcb, board_one_teensy_22.kicad_sch]
2024-01-03 PRISM FC built without errors
    [board_one_teensy_22.kicad_pcb, board_one_teensy_22.kicad_sch]
2024-01-03 Fix SD Detect error
    [board_one_teensy_22.kicad_pcb, board_one_teensy_22.kicad_sch]
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2024-01-04 update Core IO schematic and first layout concept
    [CoreIO.kicad_pcb, CoreIO.kicad_sch]
2024-01-07 fixed stepper wiring
    [CoreIO.kicad_pcb, CoreIO.kicad_sch, board_one_teensy_22.kicad_sch]
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2024-01-10 Fix problem with 3V3 plane
    [board_one_teensy_22.kicad_pcb]
2024-01-10 Fix silkscreen issue in PRISM FC
    [board_one_teensy_22.kicad_pcb]
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2024-01-10 Save backup of GS Radio before new layout
    [antenna_board.kicad_pcb, antenna_board.kicad_sch]
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2024-01-13 Add logo and switch displays to HSPI radio
    [antenna_board.kicad_pcb, antenna_board.kicad_sch]
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2024-01-14 Add big buzzer to FC
    [board_one_teensy_22.kicad_pcb, board_one_teensy_22.kicad_sch]
2024-01-14 Add two buzzers to FC
    [board_one_teensy_22.kicad_pcb, board_one_teensy_22.kicad_sch]
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2024-01-19 Changed capacitor
    Changed the large capacitor for the voltage regulator to reflect BOM
    [antenna_board.kicad_pcb, antenna_board.kicad_sch]
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2024-01-23 Fixed GPS breakout schematic pin assignment and updated board to update traces
    [board_one_teensy_22.kicad_pcb, board_one_teensy_22.kicad_sch]
2024-01-25 Fixed Silkscreen and removed power plane
    [CoreIO.kicad_pcb, board_one_teensy_22.kicad_pcb]
2024-01-25 Add voltage divider to measure battery voltage
    Added a voltage divider and connected it to one of the analog input pins of the ESP32 so we can actually measure the battery voltage
    [antenna_board.kicad_pcb, antenna_board.kicad_sch, bom.csv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]
2024-01-25 Added 3.3V line and fixed analog routing issues on Teensy
    [board_one_teensy_22.kicad_pcb, board_one_teensy_22.kicad_sch]
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2024-01-25 Updated Core IO connectors to match updated Teensy board and change stepper to 3.3V
    [CoreIO.kicad_pcb, CoreIO.kicad_sch]
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2024-01-25 Fix silk on IO
    [CoreIO.kicad_pcb]
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2024-02-21 Updated Rev4 based on new changes to components
    Combined EAST and Prism. Updated IMU class with appropriate IMU. Added code for buzzer.
    [PRISM_main.ino, gps_class.cpp, imu_class.cpp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]
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2024-03-11 Fixing some errors, still some left
    [PRISM_main.ino, data_class.cpp, gps_class.cpp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]
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2024-04-15 Radio Class Fixes
    Mostly Fixed Radio Class, still having issues RF95
    [PRISM_main.ino, data_class.cpp, gps_class.cpp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]
2024-04-16 Code runs no errors, leds broken
    [PRISM_main.ino, data_class.cpp, gps_class.cpp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]
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2024-04-16 Something's wrong with sendRadio
    [PRISM_main.ino, data_class.cpp, gps_class.cpp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]
2024-04-16 Fix radio crash error
    [PRISM_main.ino, radio_class.cpp]
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2025-01-26 fixed latch
    [BT_01.SLDPRT, MAIN.SLDASM]
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2025-05-04 Fixed issues with stepper class
    [PRISM_main.ino, radio_class.cpp, stepper_class.cpp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]

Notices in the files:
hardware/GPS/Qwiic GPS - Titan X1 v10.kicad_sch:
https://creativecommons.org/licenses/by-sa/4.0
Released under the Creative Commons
